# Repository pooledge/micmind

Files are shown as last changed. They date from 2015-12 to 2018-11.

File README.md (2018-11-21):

# Micmind - remotely controlled microphone stand prototype (Air P3)
Arduino based microphone stand controlled remotely within a Max/MSP built standalone application. Micmind Air uses a pair of XBee Pro 868 operating in API mode for wireless communication.

This repository includes:
* Arduino sketch to upload on a Pro Mini 328 (5V)
* MaxMSP patch to build a standalone host application for Mac or Windows
* EAGLE files containing schematic and board layouts
* OpenSCAD file enclosure model to build and export in STL format for futher 3D printing
* Xbee firmware XML files used by XCTU
* XML file containing some commands for developing and debuging purposes in XCTU
* Icon file and its .psd source used for the Macintosh standalone

Software versions used at the time building the prototype:
* Mac OS X 10.9.5
* Arduino 1.0.6
* MaxMSP 5.1.3
* EAGLE 7.2.0
* OpenSCAD 2015.03-1
* XCTU 6.2.0
* Photoshop CS6

## What is it about?

Micmind is simply a microphone stand for seamless indoor stereo recording, controlled remotely. So called AB-stereo technique, commonly used in classical music recording utilizes a pair of omnidirectional microphones. While collecting both time-of-arrival and level difference information and being very efficient, this method demands considerations and decisions often being made on-the-fly, also involving some sort of luck. While familiar with theory, sound engineer may still play quite a long time with a stand position and the distance between two microphones as those factors have dramatic impact on the sound image. Very often classical recordings are made with AB only and within low-time conditions, especially those low paid sound engineer jobs if you know what I mean. Now, to tell a long story short, being able to adjust AB parameters from some distance brings following advantages:
* The need to cover multiple meters between control and recording rooms is eliminated (meh)
* Key adjustments applied on-the-fly with their effect to be observed instantly, thus not only the result is achieved in a more efficient way but also the learn effect of using this recording technique increases dramatically.

Micmind is not pretending to be unique, as of 2016 there are different similar products currently available: Remote-Mast, Robo-Mic, Stereoblade, Optogate... etc. However each of them has their disadvantages: summed up they are either too bulky, expensive, loud or not suitable for AB recording due to its size or construction principles.

## Key features
* Up to 1.2km line-of-sight controlling distance
* No frames, rails or cables - end position is freely adjustable
* Linear and rotation movement modes
* Stereo base distance adjustment from 1cm to 99cm
* Impact noise isolation
* Virtual capacitor technology for smoother motion
* Simple and robust modular construction
* Stable grip and low-noise operation

## Safety
* Permanent motor braking while stall
* Panic mode if connection to host computer is lost or not available
* Clear visual status indication both host- and client-side

## Power management
* Single 6c lithium-polymer battery for hours of operation, 5Ah, built-in
* Seamless charging with no disassembly
* Operation/charging mode selector switch

## Chassis
* Main stand built upon freely available Manfrotto 1005BAC tripod and 100mm mecanum wheels
* Simple and efficient 24VDC motors

## Future demands
* ~~Future of Micmind is the future of wireless microphoning. Though our wired initial prototype already serves at it's best, imagine a microphone stand, that can move freely, with no cables, with no boundaries.~~
* ~~Along the embedding of an Xbee modules both host- and client-side for seamless and stable communication, a non-wired future release of Micmind also demands some wireless components to transmit audio signals from floating microphones.~~
* Though a mechanism for height adjustment was initially planned, it was dropped later, as it wasn't possible to retrieve such a non-bulky, low-load, high-stroke component as a serial produced unit. A custom build of a telescopic pipe however may solve this problem, bringing to life an amazing possibility to adjust microphones' position in absolutely all extents without dramatically reducing stand's mobility and stability. 
* Since a homo drive proved to be the right choice for a moveable mic stand, even slightly bigger wheels will instantly allow more stability and better weight distribution - for preciser handling when overcoming boundaries such as cables, height differences of various surfaces and their defects.
* Quieter motors is just a matter of costs, since all their characteristics are already known and have been proved as appropriate. Using gearless motors instead of geared ones might be a good decision, the more so, because the programmable hardware layer of Micmind easily allows their embedding. In that way it is definitely possible to achieve a smoother operation with significant lower noise emission - an important factor for recording classical music known for its wide dynamic range and low SNR.
* ~~PCB, a printed circuit board. This text's author spent two weeks soldering a circuit board for the prototype. Involving more components in the future simply won't leave any choice on this one. For the efficiency of work!~~
* Undo/redo functionality for fast A/B testing

## Disclaimer
This project is being realized as a part of the master degree diploma at the sound engineering faculty of University of music and performing arts in Vienna, Austria.
This disclaimer is being updated constantly along required regulations.

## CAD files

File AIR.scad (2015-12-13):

// Global
$fn=100;
thickness=1.2;

/*********************************** Setup ***********************************/

// Exterior Dimensions
height=170;
length=109;
width=68;
bodyRadius=200;

// Interior dimensions
switchWallLength=25;
switchWallDistance=24;
supportWallHeight=10;
supportWallLength=72;
boardWallHeight=110;

// Other Variables
switchHoleRadius=10;
ledHoleRadius=1.5;
xlrHoleRadius=11.8;
xlrmHoleRadius=6;
sideHoleMargin=20;
sideHoleRadius=15;
sideHoleLength=length-2*sideHoleRadius-sideHoleMargin*2;
sideHoleHeight=height-2*sideHoleMargin-2*sideHoleRadius;
kRubinstein=8; // =)
kOverprint=0.25;
legoHoleRadius=2.4;

// Body Exterior
module sideWall(topBottomThickness){
    translate([0,-5,0]){
        intersection(){
            translate([-bodyRadius,-15,0]){
                difference() {
                    cylinder(h=height, r=bodyRadius, $fn=1000);
                    translate([0,0,topBottomThickness*thickness]){
                        cylinder(h=height-2*topBottomThickness*thickness, r=(bodyRadius-thickness));
                    }
                    rotate(180){
                        translate([5,0,0]){
                            cube([2*bodyRadius-width,2*bodyRadius,height*3], center=true);
                        }
                    }
                }  
            }
            translate([0,5,0]){
                cube([2*bodyRadius,length,2*height],center=true);
            }
        } 
    }
}

module hook(){
    difference(){
        cube([1.5*kRubinstein,1.5*kRubinstein,kRubinstein*2],center=true);
        translate([-kRubinstein/4,kRubinstein/4,0]){
            cube([kRubinstein,kRubinstein,kRubinstein*2],center=true);
        }
        translate([0,-kRubinstein/2,-kRubinstein*1.5]){
            rotate([45,0,0]){
                cube([kRubinstein*1.5,kRubinstein*2,kRubinstein*3],center=true);
            }
        }
    }
}

module hooks(){
    translate([-3*kRubinstein,-length/2-kRubinstein*0.75,height-switchWallLength]){
        hook();
    }
    translate([3*kRubinstein,-length/2-kRubinstein*0.75,height-switchWallLength]){
        mirror([1,0,0]){
            hook();
        }
    }
    translate([-3*kRubinstein,-length/2-kRubinstein*0.75,switchWallLength/2]){
        hook();
    }
    translate([3*kRubinstein,-length/2-kRubinstein*0.75,switchWallLength/2]){
        mirror([1,0,0]){
            hook();
        }
    }
}

module exteriorComponents(topBottomThickness){
    translate([width/2,0,0]){
        sideWall(topBottomThickness);
    }
    translate([-width/2,0,0]){
        mirror([1,0,0]){
            sideWall(topBottomThickness);
        }
    }
    
    // Front wall
    translate([0,length/2-thickness/2,height/2]){
        cube([39,thickness,height],center=true);
    }
    
    // Back wall
    #translate([0,-length/2+thickness/2,height/2]){
        cube([61.5,thickness,height],center=true);
    }
}

module exterior(topBottomThickness=1){
    
    // Back gutter cut-in
    difference(){
        exteriorComponents(topBottomThickness);
            translate([0,-length/2-kRubinstein/1.5,-kRubinstein/2]){
            cylinder(r=kRubinstein*1.1,h=height+kRubinstein);
        }
    }
    difference(){
        translate([0,-length/2-kRubinstein/1.5,-kRubinstein]){
            difference(){
                cylinder(r=kRubinstein*1.2,h=height+kRubinstein);
                cylinder(r=kRubinstein*1.2-thickness,h=height+kRubinstein);
            }
        }
        translate([0,-length/2-kRubinstein,height/2-kRubinstein/2]){
            cube([width,2*kRubinstein,height+kRubinstein],center=true);
        }
        translate([0,0,-kRubinstein/2]){
            cube([1.5*width,1.5*length,kRubinstein],center=true);
        }
    }
}

// Body Interior
module switchWall() {
    difference(){
        cube([thickness,switchWallLength,height],center=true);
        translate([0,-switchWallLength/2+3,height/2-(height-boardWallHeight)/2]){
            cube([thickness*2,6,height-boardWallHeight],center=true);
        }
    }
}

module switchWalls() {
    translate([(switchWallDistance+thickness)/-2,length/2-switchWallLength/2,height/2]){
        switchWall();
    }
    translate([(switchWallDistance+thickness)/2,length/2-switchWallLength/2,height/2]){
        switchWall();
    }
}

module supportWall() {
    cube([thickness,supportWallLength,supportWallHeight],center=true);
}

module supportWalls() {  
    translate([(switchWallDistance+thickness)/2,length/2-supportWallLength/2,supportWallHeight/2]){
        supportWall();
    }
    translate([(switchWallDistance+thickness)/-2,length/2-supportWallLength/2,supportWallHeight/2]){
        supportWall();
    }  
}

module boardWall() {
    difference(){
        translate([width/-2+thickness*0.75,length/2-supportWallLength,supportWallHeight]){
            cube([width-1.5*thickness,thickness,boardWallHeight]);
        }
        /*translate([1.8*kRubinstein,-15,height-(height-123-2*kRubinstein)]){
            cube([2*kRubinstein,thickness*10,height-120],center=true);
            /*minkowski(){
                cube([1,thickness*10,height-120-2*kRubinstein],center=true);
                rotate([90]){
                    cylinder(h=thickness*10, r=kRubinstein);
                }
            }
        }*/
        /*translate([-1.8*kRubinstein,-15,height-(height-123-2*kRubinstein)]){
            cube([2*kRubinstein,thickness*10,height-120],center=true);
            /*minkowski(){
                cube([1,thickness*10,height-120-2*kRubinstein],center=true);
                rotate([90]){
                    cylinder(h=thickness*10, r=kRubinstein);
                }
            }
        }*/
        
        // Board rigging holes
        translate([18,-8,37]){
            rotate([90]){
                cylinder(h=thickness*10, r=legoHoleRadius+kOverprint);
            }
        }
        translate([18,-8,114]){
            rotate([90]){
                cylinder(h=thickness*10, r=legoHoleRadius+kOverprint);
            }
        }
    }
    
    // Battery placeholders and strength'tens
    translate([-switchWallDistance/2-thickness/2,length/2-supportWallLength+thickness/2+1,boardWallHeight/2+supportWallHeight]){
        cube([thickness,thickness+2,boardWallHeight],center=true);
    }
    translate([switchWallDistance/2+thickness/2,length/2-supportWallLength+thickness/2+1,boardWallHeight/2+supportWallHeight]){
        cube([thickness,thickness+2,boardWallHeight],center=true);
    }
    #translate([-27,length/2-supportWallLength+thickness/2-2+kOverprint/2,boardWallHeight/2+supportWallHeight]){
        cube([2,thickness+4-kOverprint,boardWallHeight],center=true);
    }
    
    // Temporary touch
    /*#translate([0,length/2-supportWallLength+thickness/2+1+40,height/2+supportWallHeight/2]){
        cube([55,thickness+2,height-supportWallHeight],center=true);
    }
    #translate([0,length/2-supportWallLength+thickness/2+1-25,height/2+supportWallHeight/2]){
        cube([63,thickness+2,height-supportWallHeight],center=true);
    }*/
      
}

module frontLoopCover() {   
    difference(){
        translate([0,length/2-switchWallLength/2,supportWallHeight]){
            cube([switchWallDistance,switchWallLength-12,supportWallHeight*2],center=true);
        }
        translate([-width/2,length/2-switchWallLength/2,supportWallHeight+1.5*thickness]){
            rotate([0,90]){
                cylinder(h=width, r=legoHoleRadius+kOverprint);
            }
        }
    } 
    translate([0,length/2-switchWallLength/2,thickness*1]){
        #cube([switchWallDistance+2*thickness,switchWallLength-12,thickness*2],center=true);
    }
}

module backLoopBodyComponent() {
    translate([-2*kRubinstein,0,0]){
        cube([kRubinstein/2,switchWallLength/2,supportWallHeight*3],center=true);
    }
    translate([2*kRubinstein,0,0]){
        cube([kRubinstein/2,switchWallLength/2,supportWallHeight*3],center=true);
    }
}

module backLoopBody() {
    translate([0,-length/2+switchWallLength/4,height-1.5*supportWallHeight]){
        difference(){
            backLoopBodyComponent();
            translate([0,switchWallLength/4,-supportWallHeight-thickness*2]){
                rotate([-45,0,0]){
                    cube([width,switchWallLength,supportWallHeight*4],center=true);
                }
            }
            translate([-width/2,0,kRubinstein]){
                rotate([0,90]){
                    cylinder(h=width, r=legoHoleRadius+kOverprint);
                }
            }
        }
    }
}
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

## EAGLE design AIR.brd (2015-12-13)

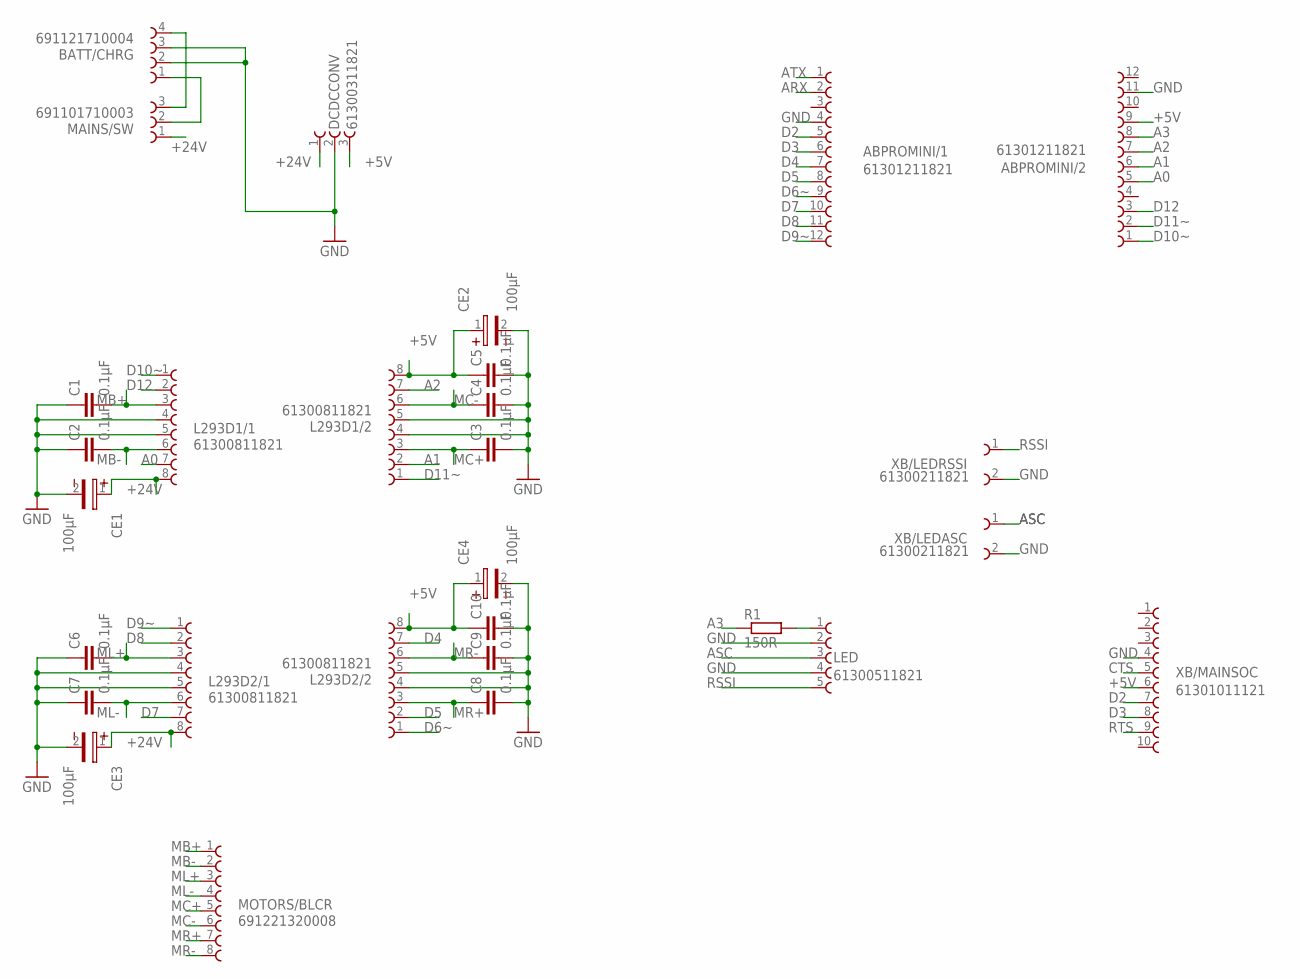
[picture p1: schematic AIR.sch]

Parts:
ABPROMINI/1, ABPROMINI/2: 61301211821
BATT/CHRG: 691121710004
C1, C2, C3, C4, C5, C6, C7, C8, C9, C10: 0.1µF; C025-025X050
CE1, CE2, CE3, CE4: 100µF; 8X3.5X0.9(DXAXB)
DCDCCONV: 61300311821
L293D1/1, L293D1/2, L293D2/1, L293D2/2: 61300811821
LED: 61300511821
MAINS/SW: 691101710003
MOTORS/BLCR: 691221320008
R1: 150R; 0204/7
XB/LEDASC: 61300211821
XB/LEDRSSI: 61300211821
XB/MAINSOC: 61301011121

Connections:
+5V: ABPROMINI/2.9, C5.1, C10.1, CE2.1, CE4.1, DCDCCONV.3, L293D1/2.8, L293D2/2.8, XB/MAINSOC.6
+24V: CE1.1, CE3.1, DCDCCONV.1, L293D1/1.8, L293D2/1.8, MAINS/SW.1
A0: ABPROMINI/2.5, L293D1/1.7
A1: ABPROMINI/2.6, L293D1/2.2
A2: ABPROMINI/2.7, L293D1/2.7
A3: ABPROMINI/2.8, R1.1
ARX: ABPROMINI/1.2
ASC: LED.3, XB/LEDASC.1
ATX: ABPROMINI/1.1
CTS: XB/MAINSOC.5
D2: ABPROMINI/1.5, XB/MAINSOC.7
D3: ABPROMINI/1.6, XB/MAINSOC.8
D4: ABPROMINI/1.7, L293D2/2.7
D5: ABPROMINI/1.8, L293D2/2.2
D6~: ABPROMINI/1.9, L293D2/2.1
D7: ABPROMINI/1.10, L293D2/1.7
D8: ABPROMINI/1.11, L293D2/1.2
D9~: ABPROMINI/1.12, L293D2/1.1
D10~: ABPROMINI/2.1, L293D1/1.1
D11~: ABPROMINI/2.2, L293D1/2.1
D12: ABPROMINI/2.3, L293D1/1.2
GND: ABPROMINI/1.4, ABPROMINI/2.11, BATT/CHRG.2, BATT/CHRG.3, C1.1, C2.1, C3.2, C4.2, C5.2, C6.1, C7.1, C8.2, C9.2, C10.2, CE1.2, CE2.2, CE3.2, CE4.2, DCDCCONV.2, L293D1/1.4, L293D1/1.5, L293D1/2.4, L293D1/2.5, L293D2/1.4, L293D2/1.5, L293D2/2.4, L293D2/2.5, LED.2, LED.4, XB/LEDASC.2, XB/LEDRSSI.2, XB/MAINSOC.4
MB+: C1.2, L293D1/1.3, MOTORS/BLCR.1
MB-: C2.2, L293D1/1.6, MOTORS/BLCR.2
MC+: C3.1, L293D1/2.3, MOTORS/BLCR.5
MC-: C4.1, L293D1/2.6, MOTORS/BLCR.6
ML+: C6.2, L293D2/1.3, MOTORS/BLCR.3
ML-: C7.2, L293D2/1.6, MOTORS/BLCR.4
MR+: C8.1, L293D2/2.3, MOTORS/BLCR.7
MR-: C9.1, L293D2/2.6, MOTORS/BLCR.8
unnamed: LED.1, R1.2
unnamed: BATT/CHRG.1, MAINS/SW.2
unnamed: BATT/CHRG.4, MAINS/SW.3
RSSI: LED.5, XB/LEDRSSI.1
RTS: XB/MAINSOC.9

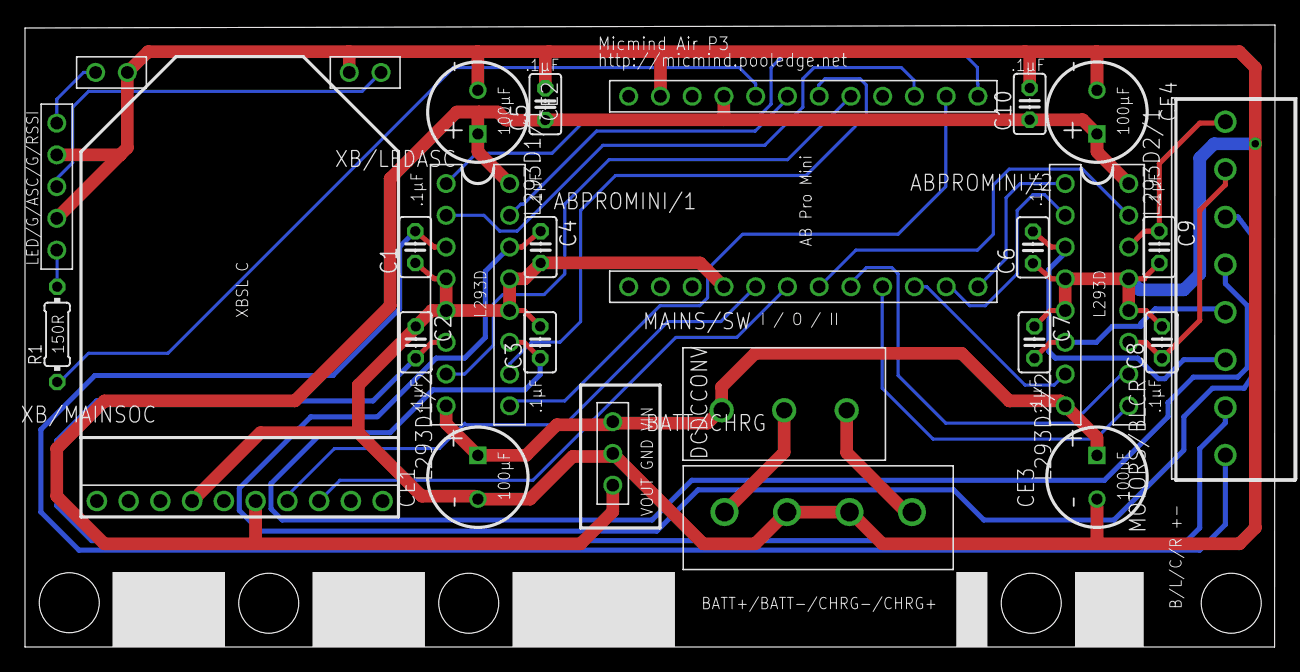
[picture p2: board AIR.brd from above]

Board: 2 copper layers, 100.0 x 49.8 mm, 29 parts (0 on the bottom side), 31 nets.

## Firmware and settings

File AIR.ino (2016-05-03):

/*  
*  Micmind Air P3 Client Unit RC
*  Version 1.1
*  
*  Implementation of Basic Interaction w/MaxMSP or Bridge Unit
*
*  Based on a sketches and patch by Thomas Ouellet Fredericks and Daniel Jolliffe
*/

#define HIGH 0x1  // Define HIGH as boolean true
#define LOW  0x0  // Define LOW as boolean false

#define asize(x) (sizeof (x) / sizeof (x[0])) // Count rows of a 2D array 

#define motorBasePower 10
#define motorBasePlus 12
#define motorBaseMinus 14
#define motorCenterPower 11
#define motorCenterPlus 15
#define motorCenterMinus 16
#define motorLeftPower 9
#define motorLeftPlus 8
#define motorLeftMinus 7
#define motorRightPower 6
#define motorRightPlus 5
#define motorRightMinus 4

#define ARX 2
#define ATX 3

#define LED 17 // red

#include <avr/power.h>
#include <avr/sleep.h>
#include <SoftwareSerial.h>
 
//=========================Declare Global Variables====================================

char currentCommand[2] = {'\0'}; // this consists of:
char MSB = 's';
byte LSB = 0;

int powerValue = 0;

long lastCommandTime = 0;
//long lastCommandThresholdForStall = 750;
long lastCommandThresholdForPanic = 1100; // corresponding to RP value @ XBee

int motorBase[3] = {motorBasePlus, motorBaseMinus, motorBasePower}; // Motors by name
int motorCenter[3] = {motorCenterPlus, motorCenterMinus, motorCenterPower};
int motorLeft[3] = {motorLeftPlus, motorLeftMinus, motorLeftPower};
int motorRight[3] = {motorRightPlus, motorRightMinus, motorRightPower};

int* motors[4] = {motorBase, motorCenter, motorLeft, motorRight}; // All of them

int leds[1] = {LED};

SoftwareSerial XBSL(ARX, ATX);

//==========================setup()==========================================
void setup() {
  
  XBSL.begin(38400);
  Serial.begin(9600);
  
  for (int i=0; i<asize(motors); i++) {  // Define all motor pins as OUTPUTs and set them to LOW
    for (int j=0; j<2; j++) {
      pinMode(motors[i][j], OUTPUT);
      digitalWrite(motors[i][j], LOW);
    }
  }
  
  for (int i=0; i<asize(leds); i++) {  // Define all LED pins as OUTPUTs and set them to LOW
    pinMode(leds[i], OUTPUT);
    digitalWrite(leds[i], LOW);
  }
  
  //Serial.println("Welcome to Micmind Air debug console!");
  //Serial.println("Now recieving XBSL output from host:");
  
}
//===========================loop()============================================
void loop() { 

  unsigned long currentTime = millis();
  
  if (XBSL.available()) {
    digitalWrite(LED, LOW);
  }
  
  if (XBSL.available()>=2) { // Gets command bytes
    for(int n=0; n<2; n++) {
      currentCommand[n] = XBSL.read(); // Fill out the command array
    }
    delay(1);
    
    // Assign
    MSB = currentCommand[0];
    LSB = currentCommand[1];
     
    powerValue = int(LSB);
      
    switch (MSB) {
      case 'c': // Rotate CW
        roam(motorCenter, false, powerValue);
        roam(motorLeft, false, powerValue);
        roam(motorRight, false, powerValue);
        break;
     case 'k': // Rotate CCW
        roam(motorCenter, true, powerValue);
        roam(motorLeft, true, powerValue);
        roam(motorRight, true, powerValue);
        break;
     case 'f': // Go forwards
        brake(motorCenter);
        roam(motorLeft, false, powerValue);
        roam(motorRight, true, powerValue);
        break;
     case 'b': // Go backwards
        brake(motorCenter);
        roam(motorLeft, true, powerValue);
        roam(motorRight, false, powerValue);
        break;
     case 'l': // Go left
        roam(motorCenter, false, powerValue);
        roam(motorLeft, true, int(powerValue / 1.5));
        roam(motorRight, false, int(powerValue / 2.8));
        break;
     case 'r': // Go right
        roam(motorCenter, true, powerValue);
        roam(motorLeft, false, int(powerValue / 1.5));
        roam(motorRight, true, int(powerValue / 2.8));
        break;
     case 'w': // Increase base
        roam(motorBase, true, powerValue);
        break;
     case 'n': // Decrease base
        roam(motorBase, false, powerValue);
        break;
     case 's':
     default:
        stall();
        break;
    }
    
    lastCommandTime = currentTime;
    Serial.print(powerValue);
    Serial.print(" ");
    Serial.print(int(powerValue / 2.2));
    Serial.print(" ");
    Serial.println(int(powerValue / 1.5));
    return;
  }
 
  /*if (currentTime - lastCommandTime >= lastCommandThresholdForStall) {
    stall();
  }*/
  if (currentTime - lastCommandTime >= lastCommandThresholdForPanic) {
    panic();
  }
  
}

//===========================custom functions============================================

void roam(int motor[], boolean dir, int power) { // Sets motor in movement
  digitalWrite(motor[0], dir);
  digitalWrite(motor[1], !dir);
  analogWrite(motor[2], power);
  //digitalWrite(LED, HIGH);
}

void brake(int motor[]) { // Brakes motor
  digitalWrite(motor[0], LOW);
  digitalWrite(motor[1], LOW);
  analogWrite(motor[2], 0); // Maybe 1 for brake?
}

void stall() { // Brakes all motors
  //digitalWrite(LED, LOW);
  for (int i=0; i<asize(motors); i++) {
    brake(motors[i]);
  }
}

void panic() { // Brakes all motors
  stall(); 
  digitalWrite(LED, HIGH);
  sleep();
}

void sleep() { // Brakes all motors and lights up the LED
  set_sleep_mode(SLEEP_MODE_IDLE);   // sleep mode is set here
  sleep_enable();          // enables the sleep bit in the mcucr register
                             // so sleep is possible. just a safety pin 
  
  power_adc_disable();
  power_spi_disable();
  power_timer0_disable();
  power_timer1_disable();
  power_timer2_disable();
  power_twi_disable();
    
  sleep_mode();            // here the device is actually put to sleep!!
 
                             // THE PROGRAM CONTINUES FROM HERE AFTER WAKING UP
  sleep_disable();         // first thing after waking from sleep:
                            // disable sleep...

  power_all_enable();
}

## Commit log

2015-05-31 Added EAGLE Files
    [AIR.brd, AIR.sch]
2015-06-01 Updated EAGLE files
    [AIR.brd, AIR.sch]
2015-06-02 First test run, awaiting flow modifications
2015-06-06 More polishing on clockery + XCTU frame examples
2015-06-12 Major UI improvements, Arduino and Max files uptd
2015-06-14 Major stability and UI improvements
    Removed calibration setting from UI, new dynamic AT frame size add-on,
    speed differentiation between roam/base, minor UI tweaka
    [AIR.ino]
2015-06-16 Major improvements on hardware, patch stability
    [AIR.brd, AIR.sch]
2015-06-17 Improved TX power level setting
2015-06-17 PCB updated for integration with LEGO
    [AIR.brd]
2015-06-18 Setting TX power level message fix
2015-11-02 Added Sketchup file for the enclosure
    [AIR.skp]
2015-11-09 SketchUp enclosure model replaced with an OpensCAD
    [AIR.scad, AIR.skp]
2015-11-21 OpenSCAD update for the enclosure
    [AIR.scad]
2015-11-27 OpenSCAD enclosure update
    [AIR.scad]
2015-12-13 Updated OpenSCAD enclosure and board
    [AIR.brd, AIR.scad]
2016-05-02 initial commit, broken apart =(
    [AIR.ino]
2016-05-03 still testing, major redesign in readAPI and others, actionUI needs fixing
    [AIR.ino]
2016-05-05 stable client connection, todo: coll!, power level

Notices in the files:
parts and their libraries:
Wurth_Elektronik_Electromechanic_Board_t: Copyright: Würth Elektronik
